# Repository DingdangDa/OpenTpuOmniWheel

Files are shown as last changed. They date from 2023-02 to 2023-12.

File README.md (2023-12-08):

# OpenTpuOmniWheel

## 为什么做这个？

在RoboMaster比赛中，全向轮作为一种实用的底盘结构，广受欢迎。

在淘宝购买全向轮的时候，大家要么选择航发**16块钱**一个的高摩擦力、不耐用的滚子，一辆车的滚子**1792块钱**；或者是轮趣6块钱一个的又硬又没有摩擦力的滚子，属于是价格与性能不可兼得。

QQ群：704988252

## 项目介绍

我开模制造聚氨酯和橡胶材质的全向轮滚子，想让大家都能够用上物美价廉的全向轮。价格**5.5元/个**和**9元/个**，包含轴承、销钉、垫片。

OTOW-Pic1

图中左边是安装了自制3508P13轮毂减速器（参考自广东工业大学）的全向轮，右边是开源的适配上交联轴器的全向轮。

这次加工的滚子尺寸与**航发**的相同，用于制作直径150mm的全向轮。

滚子的销钉/轴，使用3个3mm板材夹在一起，建议使用M3\*13螺丝固定（该尺寸不常见，在佰瑞特能买到），使用M3\*14也可以。

14个滚子一组，两组滚子的碳板间距11mm。左图两组之间使用了3mm连轴板材与8mm打印件垫块，右图两组之间使用了4mm连轴板材与7mm打印件垫块。

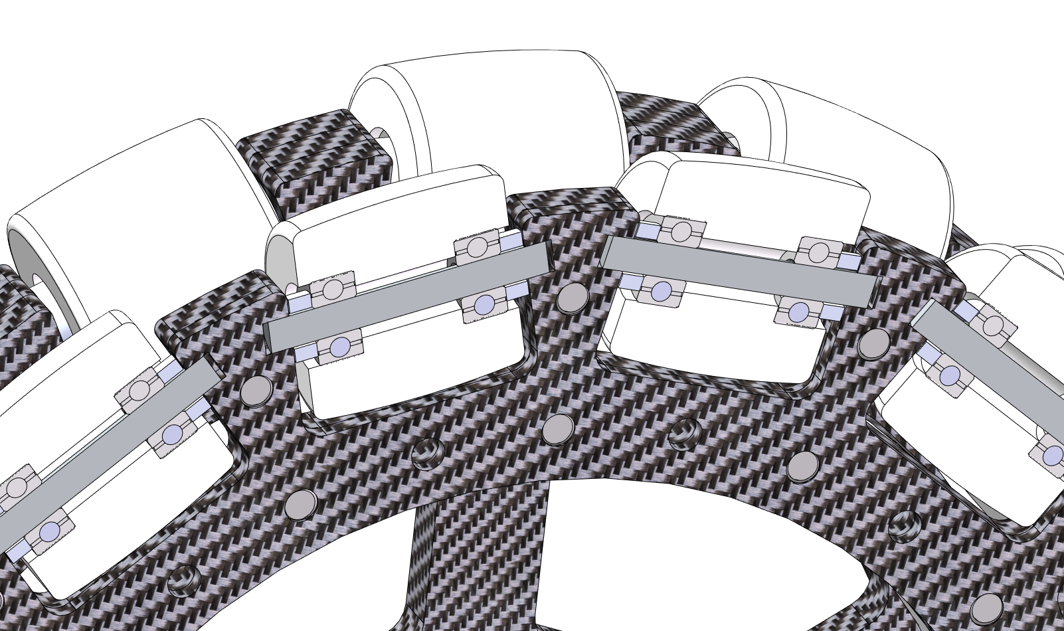
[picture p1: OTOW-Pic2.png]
OTOW-Pic2


滚子的结构如上图所示，由2个3\*8\*4轴承支撑滚子，与碳板之间是2个铝3.4\*6\*2垫片

板材堆叠后厚度为3+3+3+11+3+3+3=29mm，推荐使用M3*35螺丝进行固定。

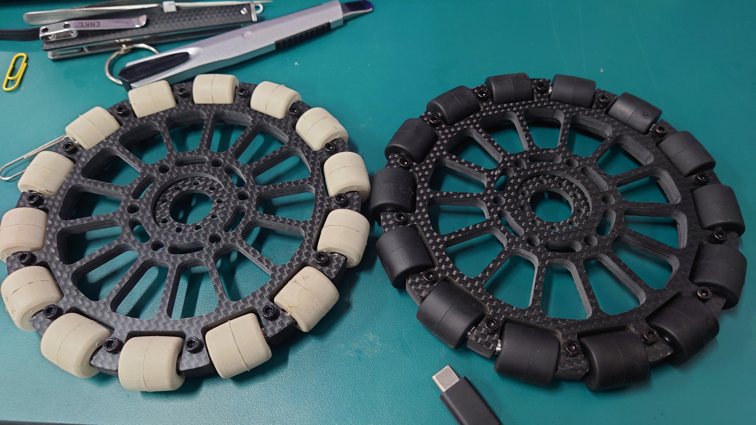
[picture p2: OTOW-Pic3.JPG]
OTOW-Pic3


## 性能

50A，聚氨酯耐用性会比橡胶的好；地胶上橡胶的摩擦力比聚氨酯好，光滑地面上聚氨酯摩擦力比橡胶的好。

## 全向轮步兵设计参考

[[机械设计]RM2022-南京理工大学-Alliance-机械结构开源-步兵机器人](https://bbs.robomaster.com/forum.php?mod=forumdisplay&fid=63&filter=typeid&typeid=11) 

## 购买

淘宝链接：（有问题到QQ群问，在淘宝问没法及时回复）

https://h5.m.taobao.com/awp/core/detail.htm?ft=t&id=706932589502

## 发票

淘宝订单后台申请

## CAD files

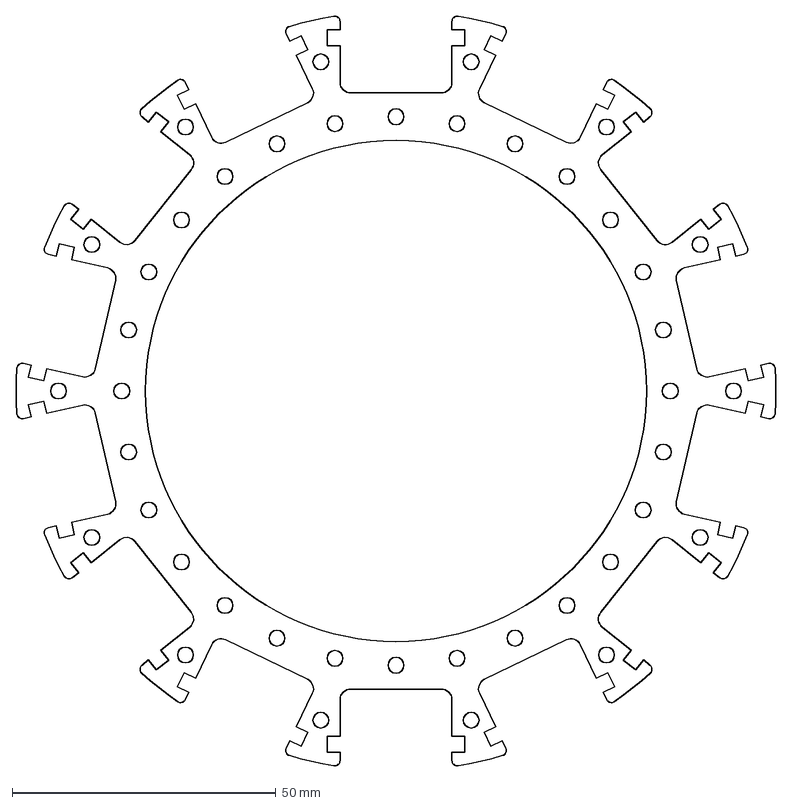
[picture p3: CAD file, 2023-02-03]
DXF&DWG/OTOW-全向轮中板-3mm.DXF
144.1 x 142.2 mm

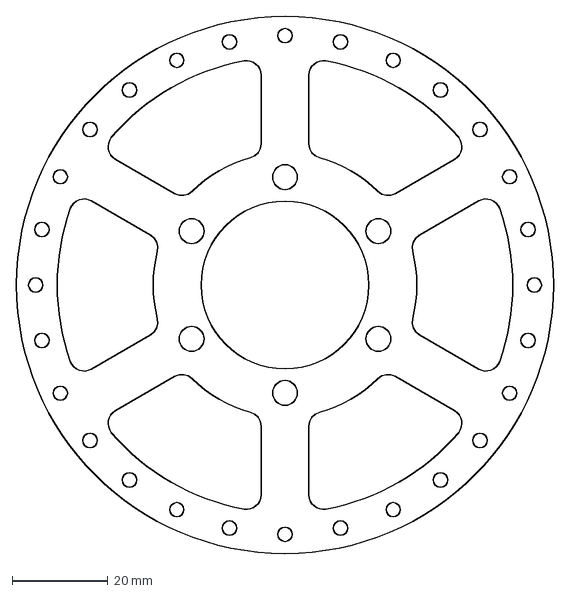
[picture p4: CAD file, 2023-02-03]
DXF&DWG/OTOW-全向轮连轴板-上交联轴器-4mm.DXF
112.0 x 112.0 mm

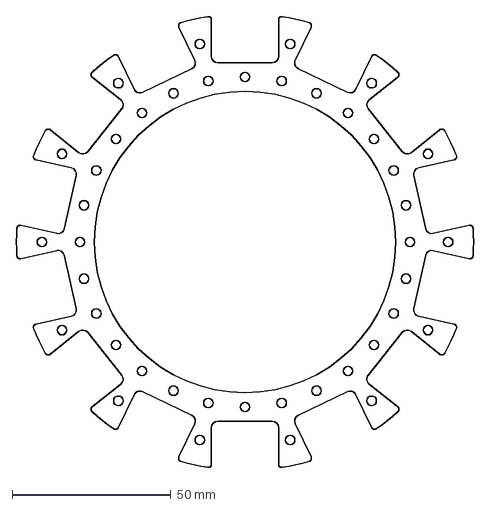
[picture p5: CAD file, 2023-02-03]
DXF&DWG/OTOW-全向轮外板-3mm.DXF
144.1 x 142.2 mm

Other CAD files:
DXF&DWG/OTOW-注塑滚子.dwg
